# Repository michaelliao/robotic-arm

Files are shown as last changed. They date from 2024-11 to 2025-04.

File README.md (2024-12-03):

# Robotic Arm

Robotic Arm是一个开源机械臂，采用ESP32-C3芯片通过PCA9685芯片控制4路舵机，使用Xbox兼容手柄遥控。

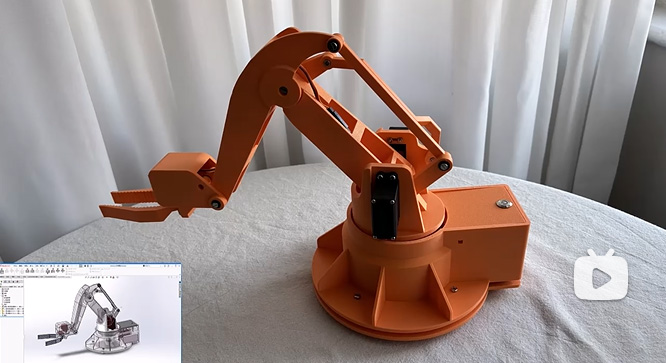
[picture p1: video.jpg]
video (https://www.bilibili.com/video/BV1EWz1YaE7P/)


## 目录结构说明

- solidworks-model：SolidWorks 2023模型源文件。
- 3d-printable：可用于3D打印的模型文件，由SolidWorks导出：
  - step：Step格式（推荐使用，如果打印机支持Step格式）。
  - stl：STL格式（通用可打印格式）。
  - 3mf：可直接打印的3D打印格式。
- esp32-controller：ESP-IDF工程源码。
- docs：相关资料。

## 设计

使用SolidWorks 2023设计建模。

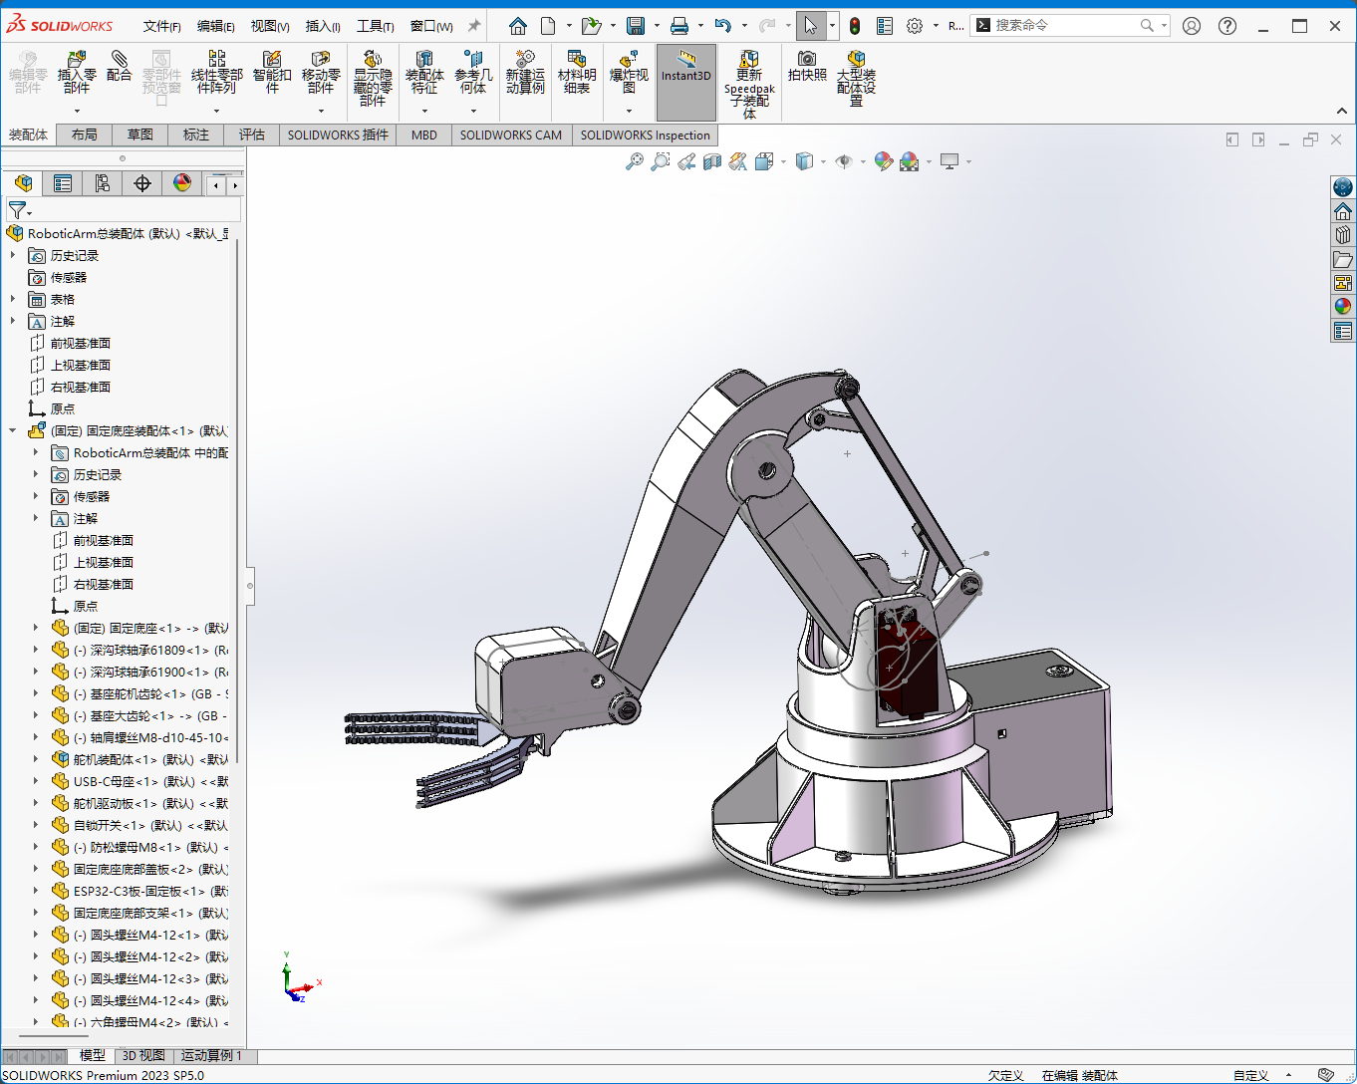
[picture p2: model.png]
solidworks-model


## 控制

使用MG996Rx3、MG90S舵机，ESP32-C3主控，PCA9685舵机驱动板，Xbox兼容手柄。

## 文档

[软件设计文档](https://liaoxuefeng.com/blogs/all/2024-12-03-robotic-arm/index.html)

## 物料清单

| 名称 | 数量 | 参考单价 (CNY) | 参考购买链接 | 说明 |
|---|---|----|---|---|
| 3D打印零件 | 1 | 70 | 使用FDM 3D打印 | 约700g PLA材料 |
| 深沟球轴承61809 | 1 | 4 | https://detail.tmall.com/item.htm?id=558165998149&skuId=3632300271694 | 固定底座旋转轴(上) |
| 深沟球轴承61900 | 1 | 1 | https://detail.tmall.com/item.htm?id=558028332089&skuId=3466348596124 | 固定底座旋转轴(下) |
| 深沟球轴承619-5 | 2 | 1 | https://detail.tmall.com/item.htm?id=665677732947&skuId=4803499105837 | 旋转底座主摇杆 |
| igus法兰轴承GFM-04050-04 | 20 | 4 | https://item.taobao.com/item.htm?id=577055358668&skuId=3973097699261 | 连接杆 |
| igus法兰轴承GFM-0506-05  | 4  | 3 | https://item.taobao.com/item.htm?id=577055358668&skuId=3917924689834 | 连接杆 |
| 轴肩螺丝M8-d10-45-10 | 1 | 3 | https://item.taobao.com/item.htm?id=727328728239&skuId=5220634259143 | 固定底座主杆 |
| 轴肩螺丝M4-d5-30-5 | 1 | 2 | https://item.taobao.com/item.htm?id=727328728239&skuId=5220634259095 | |
| 轴肩螺丝M4-d5-20-5 | 1 | 1 | https://item.taobao.com/item.htm?id=727328728239&skuId=5220634259093 | |
| 轴肩螺丝M3-d4-20-4 | 3 | 2 | https://item.taobao.com/item.htm?id=727328728239&skuId=5220634259082 | |
| 轴肩螺丝M3-d4-12-4 | 7 | 2 | https://item.taobao.com/item.htm?id=727328728239&skuId=5220634259079 | |
| 防松螺母M8 | 1 | 1 | https://item.taobao.com/item.htm?id=39801137771&skuId=3179651418712 | |
| 防松螺母M4 | 2 | 1 | https://item.taobao.com/item.htm?id=39801137771&skuId=3179651418702 | |
| 防松螺母M3 | 10 | 1 | https://item.taobao.com/item.htm?id=39801137771&skuId=3179651418705 | |
| 圆头螺丝M4-12 | 4 | 1 | https://item.taobao.com/item.html?id=559706384805&skuId=4924704353913 | |
| 圆头螺丝M2.5-12 | 12 | 1 | https://item.taobao.com/item.html?id=559706384805&skuId=4924704353893 | 用于安装MG996R舵机 |
| 圆头螺丝M2-20 | 2 | 1 | https://item.taobao.com/item.html?id=559706384805&skuId=4924704353971 | 用于安装MG90S舵机 |
| 圆头螺丝M2-8 | 2 | 1 | https://item.taobao.com/item.html?id=559706384805&skuId=4924704353888 | |
| 六角螺母M4 | 4 | 1 | https://item.taobao.com/item.htm?id=39801137771&skuId=3179651418702 | |
| 六角螺母M2.5 | 12 | 1 | https://item.taobao.com/item.htm?id=39801137771&skuId=3179950216671 | |
| 六角螺母M2 | 2 | 1 | https://item.taobao.com/item.htm?id=39801137771&skuId=3179950216672 | |
| MG90S/180度 | 1 | 17  | https://detail.tmall.com/item.htm?id=530629424244&skuId=4179287423050 | 用于前爪的微型舵机 |
| MG996R/180度 | 3 | 23  | https://detail.tmall.com/item.htm?id=530629424244&skuId=4179287423040 | 用于固定底座和移动底座的小型舵机 |
| ESP32-C3开发板 | 1 | 20 | https://detail.tmall.com/item.htm?id=802840084513&skuId=5465032488648 | 机械臂控制MCU，内置WiFi/2.4G和蓝牙BLE 5 |
| 16路PWM舵机驱动板 | 1 | 27 | https://detail.tmall.com/item.htm?id=624505789589&skuId=5054325653554 | 使用I2C接口的舵机驱动板，最多能同时驱动16路舵机 |
| 固定卡扣 | 1 | 6 | https://item.taobao.com/item.htm?id=812206553246&skuId=5676343543601 | 将机械臂固定在桌面 |
| 12mm自锁开关 | 1 | 5 | https://detail.tmall.com/item.htm?id=607769066907&skuId=5258355114246 | 机械臂电源开关 |
| 12mm自锁开关连接器 | 1 | 2 | https://detail.tmall.com/item.htm?id=607769066907&skuId=4419711093384 | 建议购买，免去焊接 |
| 盖世小鸡启明星游戏手柄 | 1 | 80 | https://detail.tmall.com/item.htm?id=749611763829&skuId=5169816701870 | Xbox兼容手柄，支持蓝牙BLE 5 |
| 10cm杜邦线 | 3 | 3 | https://detail.tmall.com/item.htm?id=14466195609 | 建议购买公对公、公对母、母对母排线，免去焊接 |

## 参考资料

- [阿奇SolidWorks教程](https://www.bilibili.com/video/BV1iw411Z7HZ/)
- [阿奇讲SolidWorks机械臂](https://www.bilibili.com/cheese/play/ss865)
- [ESP32教程（基于ESP-IDF）](https://www.bilibili.com/video/BV1eRg7exEcT/)
- [乐鑫全球开发者大会｜嵌入式系统中的低功耗蓝牙开发](https://www.bilibili.com/video/BV1kh4y1Y7GU/)
- [ESP32 PWM Driver](https://github.com/brainelectronics/esp32-pca9685)

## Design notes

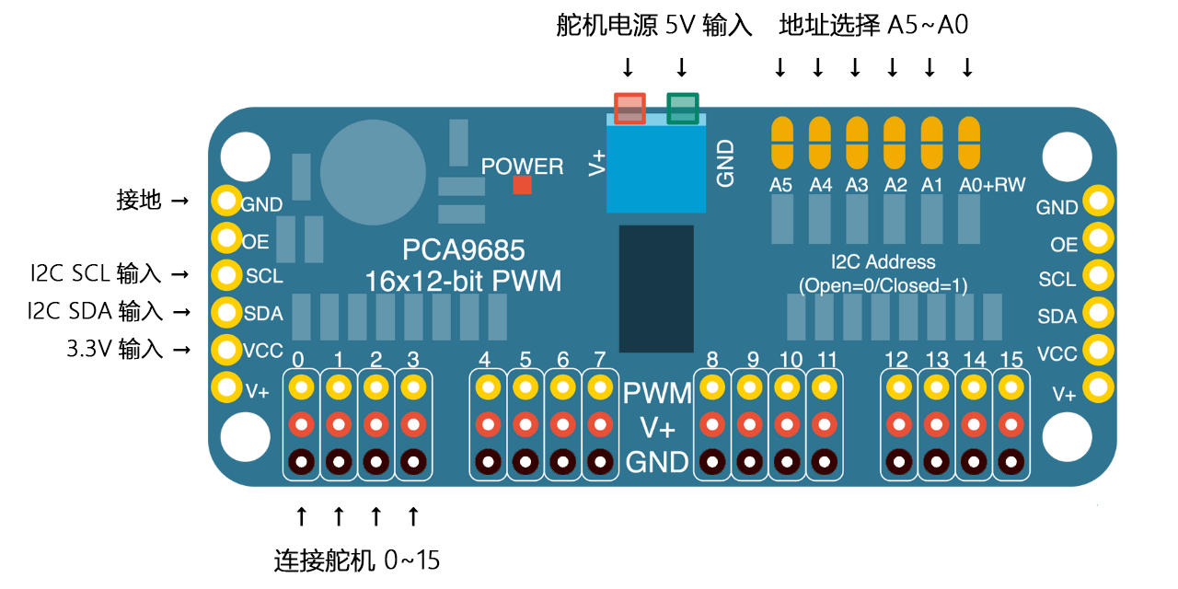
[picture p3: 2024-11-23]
docs/pca9685.png

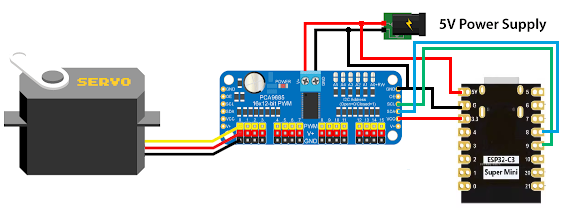
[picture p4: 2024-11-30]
docs/esp32c3-pca9685-servo.png

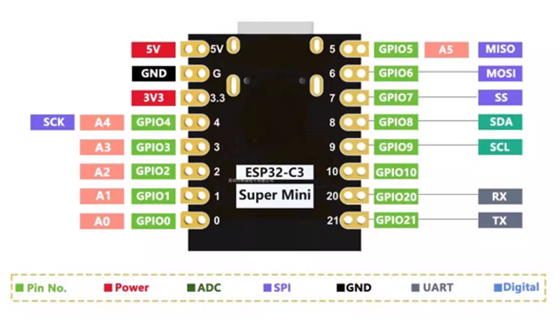
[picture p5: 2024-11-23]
docs/esp32c3.png

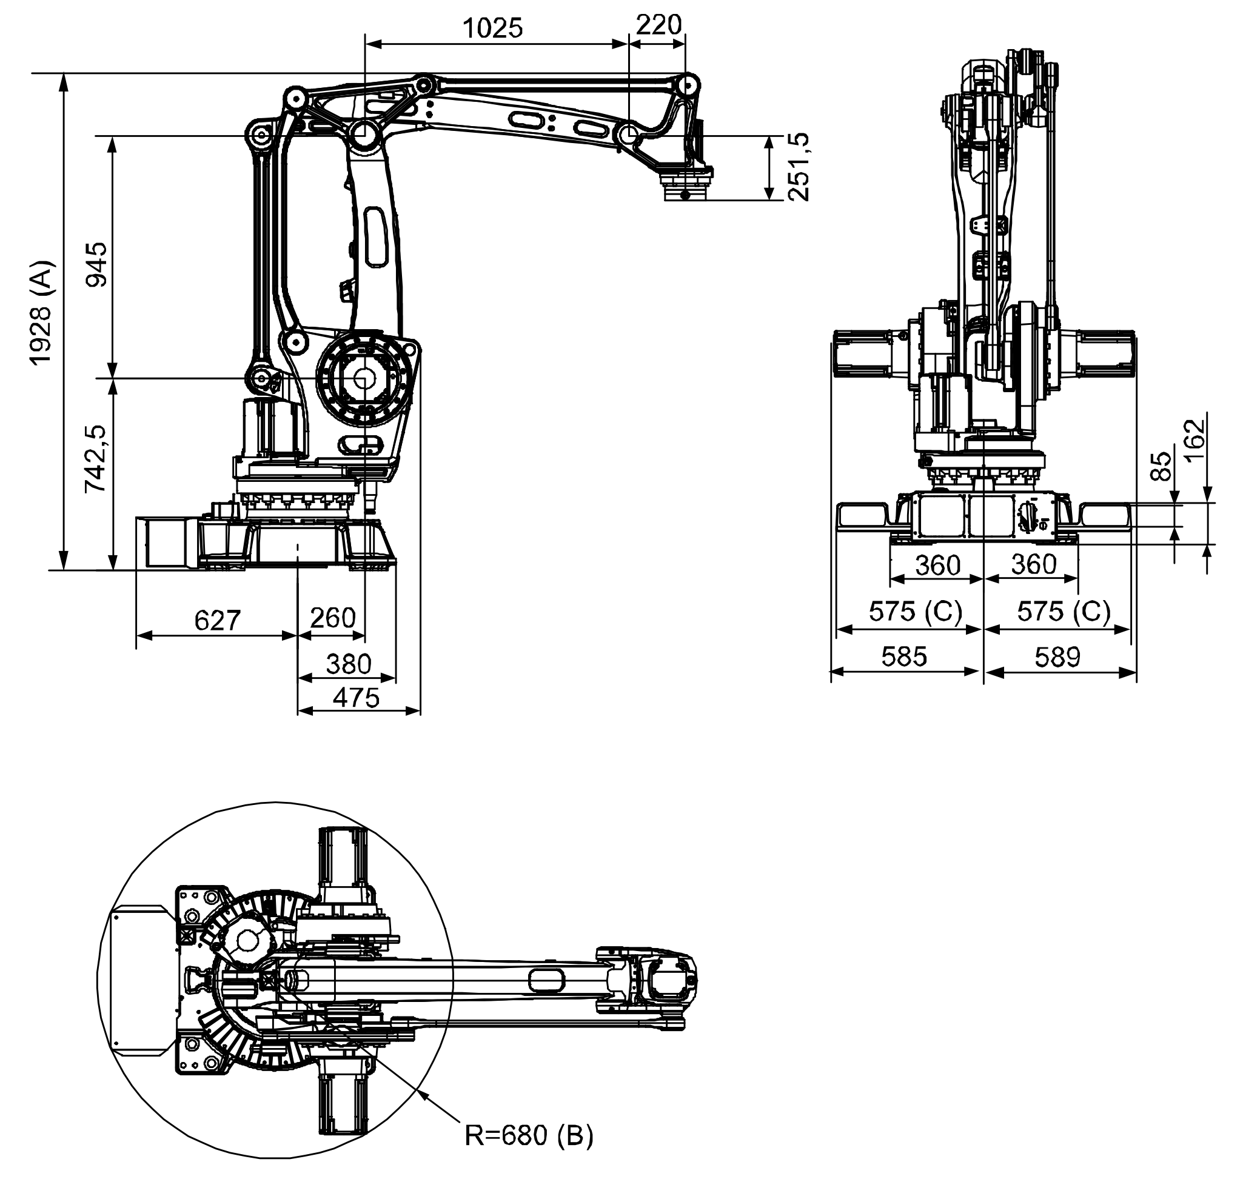
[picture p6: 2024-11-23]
docs/irb-460.png

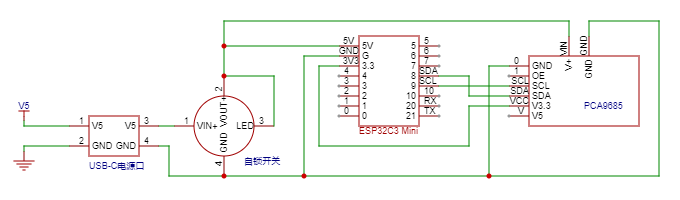
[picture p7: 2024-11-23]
docs/电路图.png

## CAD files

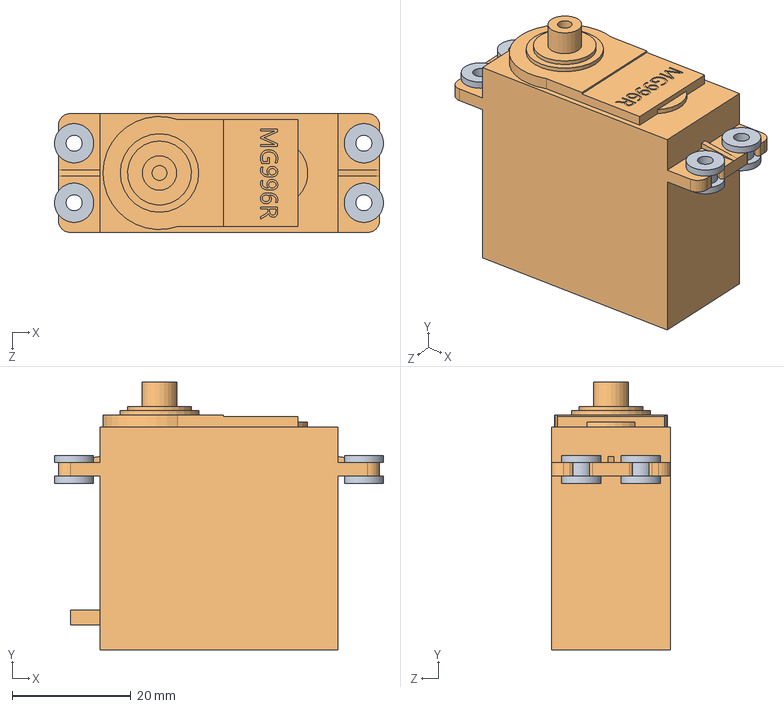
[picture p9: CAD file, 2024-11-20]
solidworks-model/舵机/舵机装配体.SLDASM
55.3 x 45.0 x 20.0 mm
MG996R
舵机橡胶圈 x 4

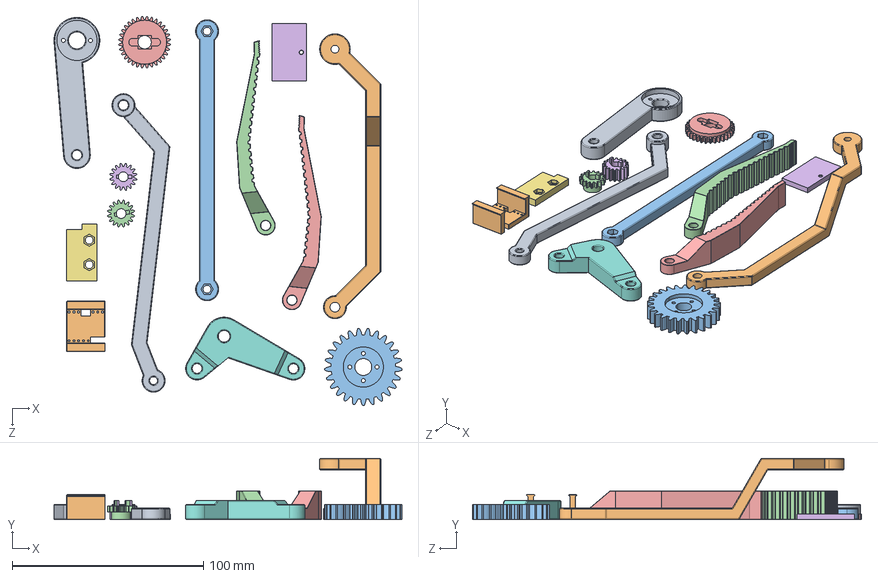
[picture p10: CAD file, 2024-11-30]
3d-printable/step/打印件2.STEP
182.1 x 32.0 x 203.8 mm
C轴摇杆
ESP32-C3板-固定板
基座舵机齿轮_GB - Spur gear 1.5M 25T 20PA 8FW ---S25A75H50L1.0N
夹爪齿轮-薄_GB - Spur gear 0.8M 16T 20PA 3FW ---S16A75H50L1.0N
夹爪齿轮-舵机_GB - Spur gear 0.8M 32T 20PA 3FW ---S32A75H50L1.0N
夹爪齿轮-厚_GB - Spur gear 0.8M 16T 20PA 7FW ---S16A75H50L1.0N
夹爪支架内部齿轮固定板
三角连杆
上水平连杆
下水平连杆
C轴连杆
夹爪C-右
夹爪C-左
夹爪支架内部舵机固定板

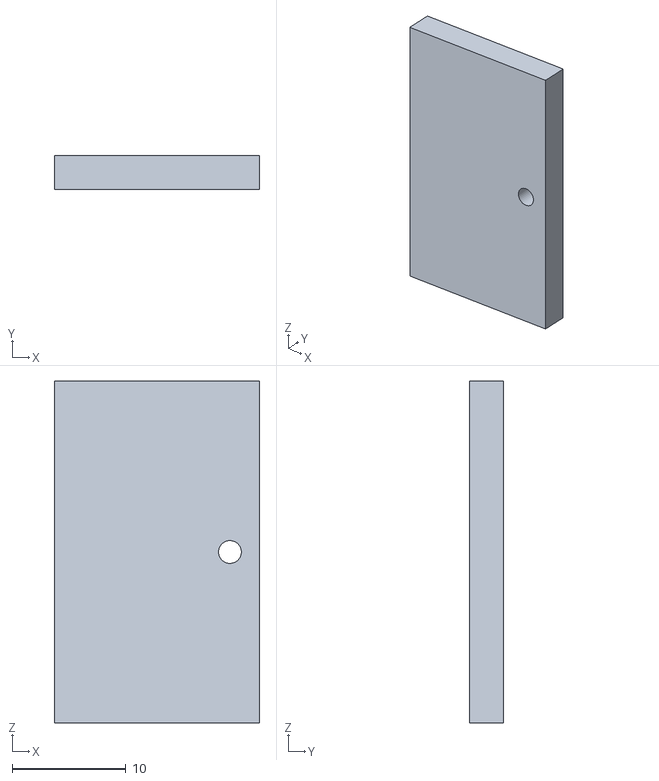
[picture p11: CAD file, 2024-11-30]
3d-printable/stl/打印装配体 - 夹爪支架内部舵机固定板-1.STL
18.0 x 3.00 x 30.0

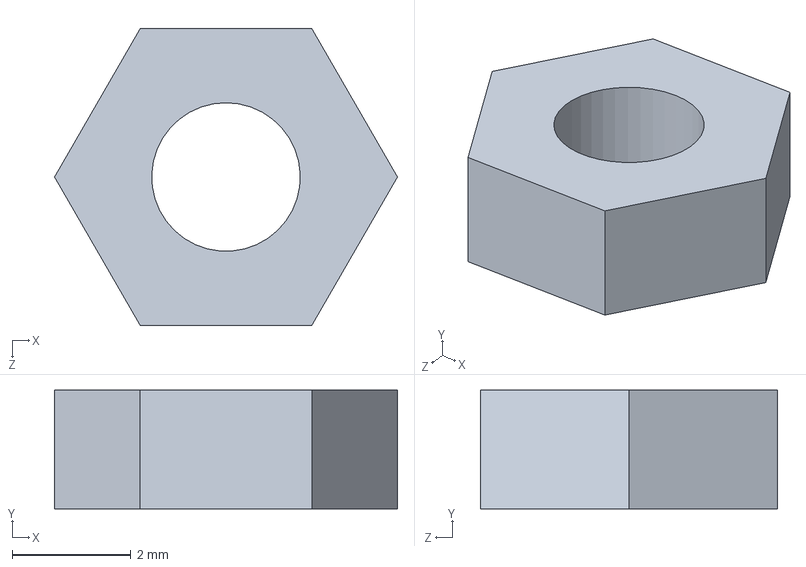
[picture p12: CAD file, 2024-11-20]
solidworks-model/五金件/六角螺母M2.5.SLDPRT
5.77 x 2.00 x 5.00 mm

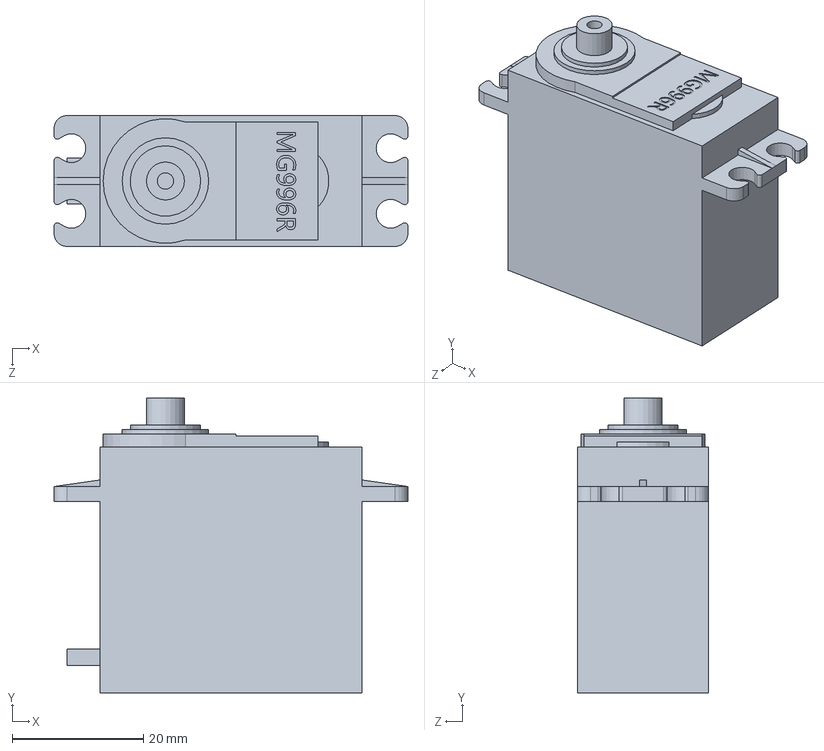
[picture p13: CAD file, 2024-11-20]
solidworks-model/舵机/MG996R.SLDPRT
54.0 x 45.0 x 20.0 mm

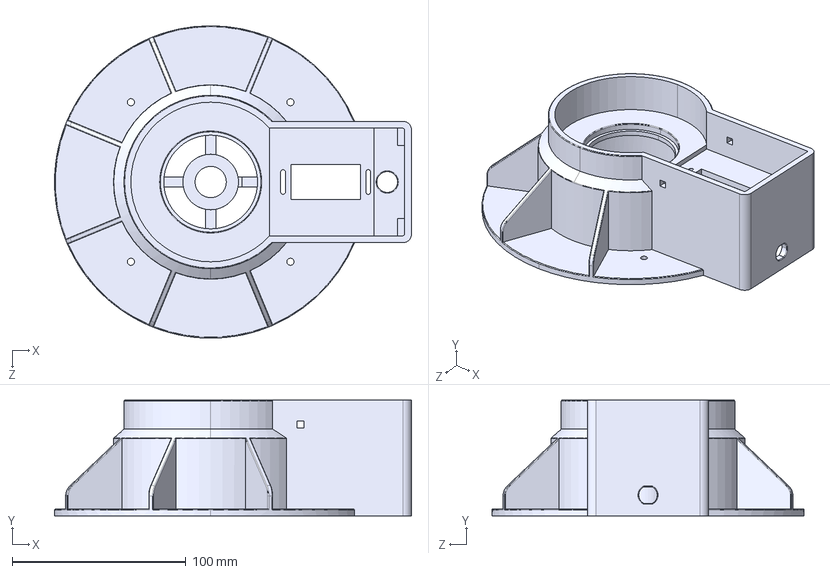
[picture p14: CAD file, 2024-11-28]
3d-printable/step/打印件1.STEP
205.7 x 66.7 x 180.0 mm

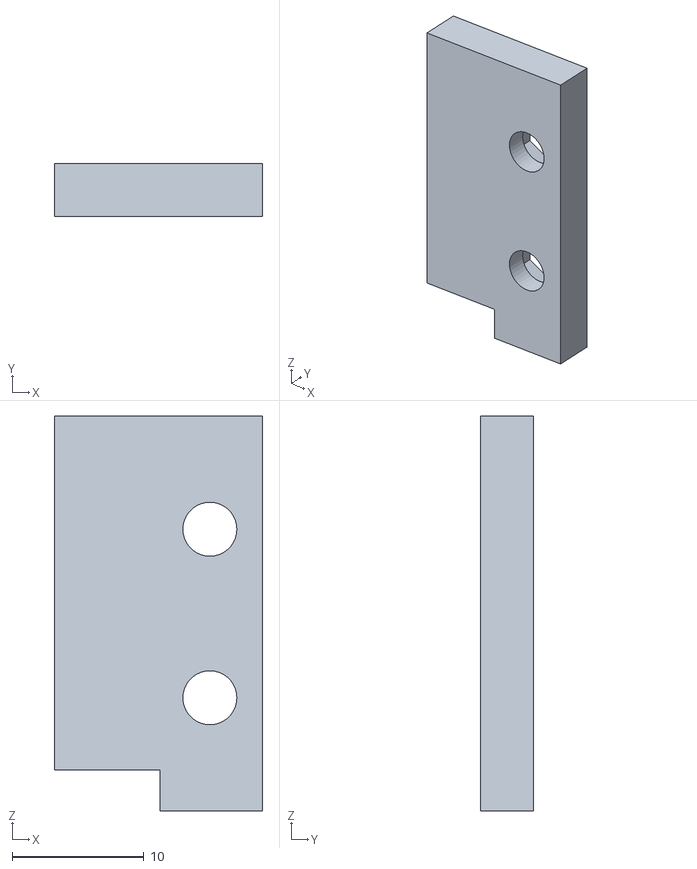
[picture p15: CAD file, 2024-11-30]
3d-printable/stl/打印装配体 - 夹爪支架内部齿轮固定板-1.STL
15.8 x 4.00 x 30.0

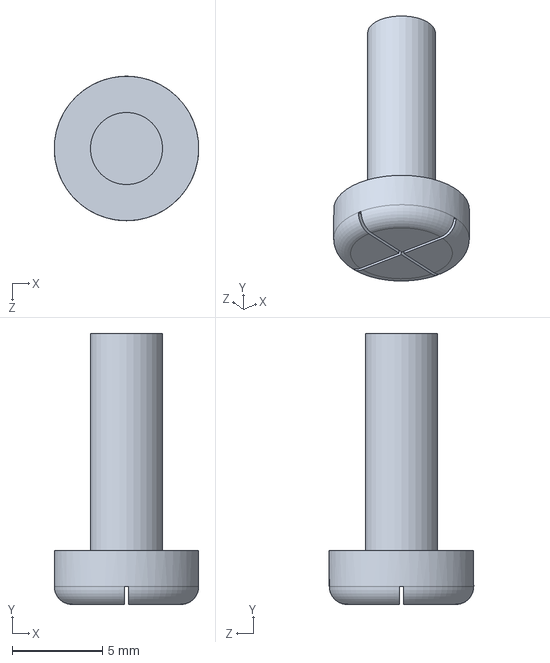
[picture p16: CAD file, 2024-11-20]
solidworks-model/五金件/圆头螺丝M4-12.SLDPRT
8.00 x 15.0 x 8.00 mm

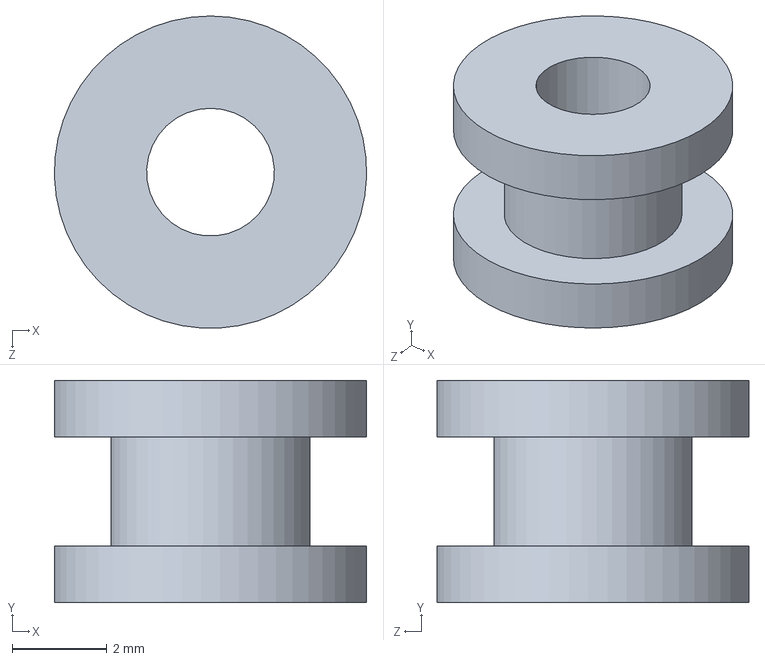
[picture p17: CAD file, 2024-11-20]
solidworks-model/舵机/舵机橡胶圈.SLDPRT
6.60 x 4.70 x 6.59 mm

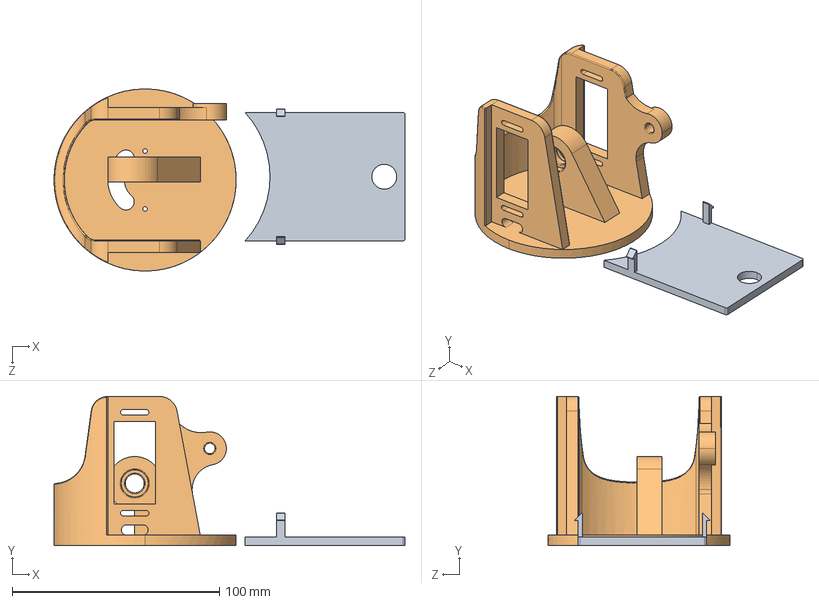
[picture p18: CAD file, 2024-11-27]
3d-printable/step/打印件6.STEP
169.5 x 72.0 x 88.0 mm
固定底座底部盖板
旋转底座

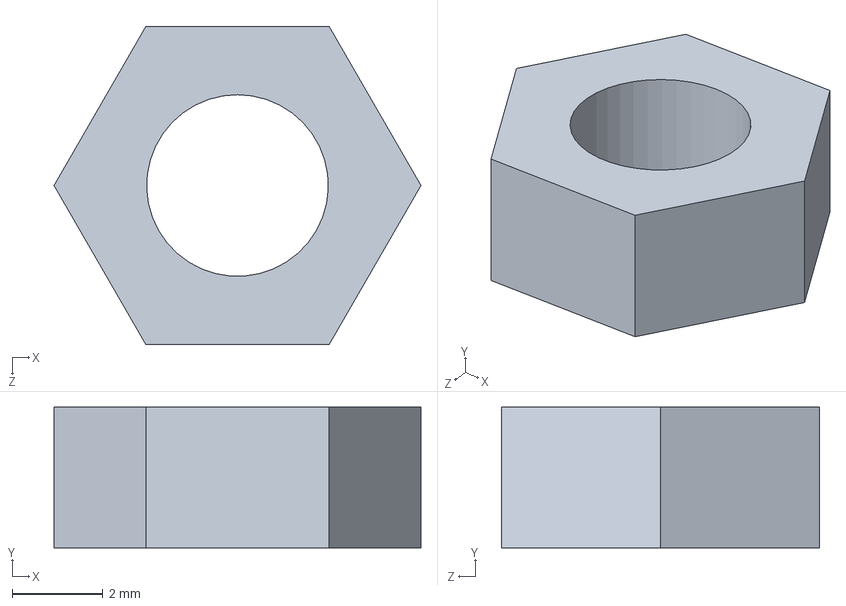
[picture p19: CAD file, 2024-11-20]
solidworks-model/五金件/六角螺母M4.SLDPRT
8.08 x 3.10 x 7.00 mm

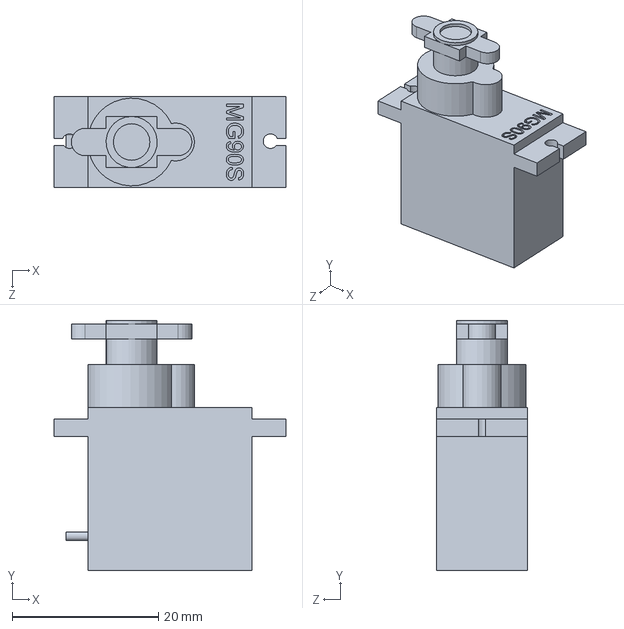
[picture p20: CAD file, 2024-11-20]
solidworks-model/舵机/MG90S.SLDPRT
31.7 x 34.2 x 12.5 mm

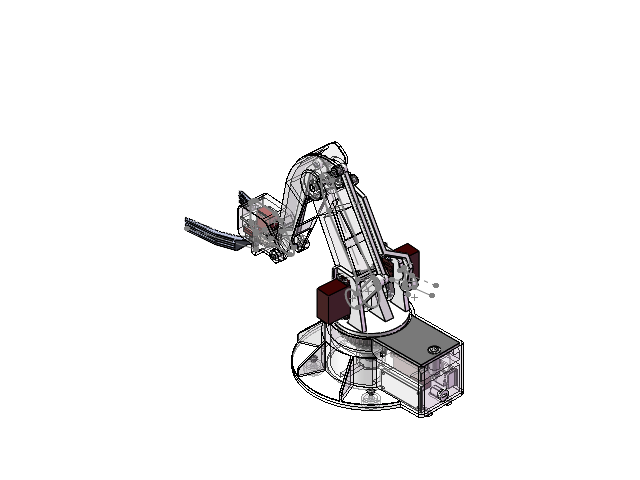
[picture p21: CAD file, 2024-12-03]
solidworks-model/RoboticArm总装配体.SLDASM
固定底座
深沟球轴承61809
深沟球轴承61900
基座舵机齿轮
基座大齿轮
轴肩螺丝M8-d10-45-10
MG996R x 3
舵机橡胶圈 x 12
舵机圆盘 x 3
USB-C母座
舵机驱动板
自锁开关
防松螺母M8
固定底座底部盖板
ESP32-C3板-固定板
固定底座底部支架
圆头螺丝M4-12 x 4
六角螺母M4 x 4
圆头螺丝M2.5-12 x 12
六角螺母M2.5 x 12
旋转底座
C轴摇杆
轴肩螺丝M4-d5-20-5
防松螺母M4 x 2
深沟球轴承619-5 x 2
BC连杆
CD连杆
C轴连杆
上水平连杆
下水平连杆
夹爪支架
MG90S
夹爪齿轮-薄
夹爪齿轮-厚
夹爪齿轮-舵机
轴肩螺丝M3-d4-20-4 x 3
防松螺母M3 x 10
轴肩螺丝M3-d4-12-4 x 7
夹爪-右
夹爪-左
夹爪支架内部齿轮固定板
圆头螺丝M2-8 x 2
夹爪支架内部舵机固定板
法兰轴承d4-GFM-04050-04 x 12
法兰轴承d5-GFM-0506-05 x 4
三角连杆
轴肩螺丝M4-d5-30-5
圆头螺丝M2-20 x 2

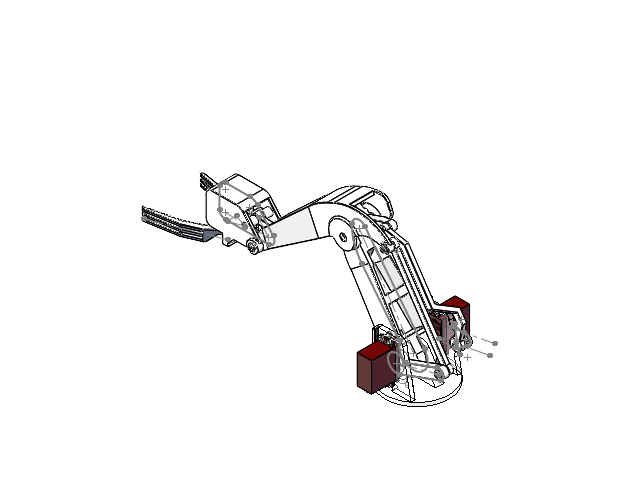
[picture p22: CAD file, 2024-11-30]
solidworks-model/旋转底座装配体.SLDASM
旋转底座
MG996R x 2
舵机橡胶圈 x 8
舵机圆盘 x 2
C轴摇杆
轴肩螺丝M4-d5-20-5
防松螺母M4 x 2
深沟球轴承619-5 x 2
BC连杆
CD连杆
C轴连杆
上水平连杆
下水平连杆
夹爪支架
MG90S
夹爪齿轮-薄
夹爪齿轮-厚
夹爪齿轮-舵机
法兰轴承d4-GFM-04050-04 x 20
轴肩螺丝M3-d4-20-4 x 3
防松螺母M3 x 10
轴肩螺丝M3-d4-12-4 x 7
夹爪-右
夹爪-左
夹爪支架内部齿轮固定板
圆头螺丝M2-8 x 2
夹爪支架内部舵机固定板
法兰轴承d5-GFM-0506-05 x 4
三角连杆
轴肩螺丝M4-d5-30-5
圆头螺丝M2.5-12 x 8
六角螺母M2.5 x 8

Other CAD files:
solidworks-model/夹爪装配体.SLDASM
solidworks-model/固定底座装配体.SLDASM
solidworks-model/打印装配体.SLDASM
3d-printable/stl/打印装配体 - 固定底座-1.STL
3d-printable/step/打印件3.STEP
3d-printable/step/打印件4.STEP
3d-printable/step/打印件5.STEP
3d-printable/step/打印测试.STEP
3d-printable/stl/打印装配体 - BC连杆-1.STL
3d-printable/stl/打印装配体 - CD连杆-1.STL
3d-printable/stl/打印装配体 - C轴摇杆-1.STL
3d-printable/stl/打印装配体 - C轴连杆-2.STL
3d-printable/stl/打印装配体 - ESP32-C3板-固定板-1.STL
3d-printable/stl/打印装配体 - 三角连杆-1.STL
3d-printable/stl/打印装配体 - 上水平连杆-1.STL
3d-printable/stl/打印装配体 - 下水平连杆-1.STL
3d-printable/stl/打印装配体 - 固定底座底部支架-1.STL
3d-printable/stl/打印装配体 - 固定底座底部盖板-1.STL
3d-printable/stl/打印装配体 - 基座大齿轮-1.STL
3d-printable/stl/打印装配体 - 基座舵机齿轮-1.STL
3d-printable/stl/打印装配体 - 夹爪C-右-1.STL
3d-printable/stl/打印装配体 - 夹爪C-左-1.STL
3d-printable/stl/打印装配体 - 夹爪支架-1.STL
3d-printable/stl/打印装配体 - 夹爪齿轮-厚-1.STL
3d-printable/stl/打印装配体 - 夹爪齿轮-舵机-1.STL
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

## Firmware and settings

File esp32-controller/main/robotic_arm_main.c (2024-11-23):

/*
 * SPDX-FileCopyrightText: 2021-2024 Espressif Systems (Shanghai) CO LTD
 *
 * SPDX-License-Identifier: Unlicense OR CC0-1.0
 */

#include <stdio.h>
#include <stdlib.h>
#include <string.h>

#include <driver/i2c.h>
#include "freertos/FreeRTOS.h"
#include "freertos/task.h"
#include "freertos/queue.h"
#include "freertos/event_groups.h"
#include "esp_chip_info.h"
#include "esp_flash.h"
#include "esp_system.h"
#include "esp_timer.h"
#include "esp_wifi.h"
#include "esp_event.h"
#include "esp_log.h"
#include "nvs_flash.h"
#include "esp_bt.h"

#if CONFIG_BT_NIMBLE_ENABLED
#include "host/ble_hs.h"
#include "nimble/nimble_port.h"
#include "nimble/nimble_port_freertos.h"
#else
#include "esp_bt_defs.h"
#include "esp_gap_ble_api.h"
#include "esp_gatts_api.h"
#include "esp_gatt_defs.h"
#include "esp_bt_main.h"
#include "esp_bt_device.h"
#endif

#if CONFIG_BT_NIMBLE_ENABLED
#include "host/ble_hs.h"
#include "nimble/nimble_port.h"
#include "nimble/nimble_port_freertos.h"
#define ESP_BD_ADDR_STR         "%02x:%02x:%02x:%02x:%02x:%02x"
#define ESP_BD_ADDR_HEX(addr)   addr[0], addr[1], addr[2], addr[3], addr[4], addr[5]
#else
#include "esp_bt_defs.h"
#include "esp_gap_ble_api.h"
#include "esp_gatts_api.h"
#include "esp_gatt_defs.h"
#include "esp_bt_main.h"
#include "esp_bt_device.h"
#endif

#include "esp_hidh.h"
#include "esp_hid_gap.h"

#include "pca9685.h"

// 注意: 将IO管脚修改为实际连接的PIN:
#define RA_I2C_MASTER_SDA_IO 8
#define RA_I2C_MASTER_SCL_IO 9

// 注意: I2C设备地址默认为0x40, 如有修改, 需改为实际地址:
#define RA_I2C_ADDRESS 0x40

// PWM频率为50Hz:
#define RA_PWM_FREQ 50

// PWM周期为20ms=20000us:
#define RA_SERVO_PWM_TIME (uint32_t)20000
// PWM脉冲时间为0.5~2.5ms=500~2500us:
#define RA_SERVO_PULSE_MIN (uint32_t)500
#define RA_SERVO_PULSE_MAX (uint32_t)2500
// 计算PWM对应的范围:
#define RA_SERVO_PWM_MIN (uint32_t)(4096 * RA_SERVO_PULSE_MIN / RA_SERVO_PWM_TIME - 1)
#define RA_SERVO_PWM_MAX (uint32_t)(4096 * RA_SERVO_PULSE_MAX / RA_SERVO_PWM_TIME - 1)
#define RA_SERVO_PWM_MID (uint32_t)((RA_SERVO_PWM_MIN + RA_SERVO_PWM_MAX) / 2)
#define RA_SERVO_PWM_RANGE (uint32_t)(RA_SERVO_PWM_MAX - RA_SERVO_PWM_MIN + 1)

// 角度范围:
#define RA_SERVO_ANGLE_RANGE (uint32_t)180

// I2C频率=100KHz:
#define RA_I2C_MASTER_FREQ 100000

// 舵机索引号:
#define RA_SERVO_A 0
#define RA_SERVO_B 1
#define RA_SERVO_C 2
#define RA_SERVO_D 3

#ifndef APP_CPU_NUM
#define APP_CPU_NUM PRO_CPU_NUM
#endif

// XBox手柄按钮:
#define XBOX_BUTTON_A 0x01
#define XBOX_BUTTON_B 0x02
#define XBOX_BUTTON_X 0x08
#define XBOX_BUTTON_Y 0x10
#define XBOX_BUTTON_L1 0x40
#define XBOX_BUTTON_R1 0x80
#define XBOX_EX_BUTTON_VIEW 0x04
#define XBOX_EX_BUTTON_MENU 0x08

#define CTRL_INPUT_DATA_LENGTH 16

#define SCAN_DURATION_SECONDS 5

static const char *TAG_HID = "HID";
static const char *TAG_PWM = "PWM";

// 根据手柄名称进行过滤,注意大小写:
static const char *CTRL_NAME = "Xbox Wireless Controller";

// 手柄输入队列:
QueueHandle_t ctrl_input_queue = NULL;

// 手柄输入数据:
// https://support.xbox.com/en-US/help/hardware-network/controller/xbox-one-wireless-controller
typedef struct __attribute__((packed)) {
    uint16_t left_stick_x; // 左摇杆
    uint16_t left_stick_y;
    uint16_t right_stick_x; // 右摇杆
    uint16_t right_stick_y;
    uint8_t left_trigger; // 左上L2按钮
    uint8_t left_trigger_level;
    uint8_t right_trigger; // 右上R2按钮
    uint8_t right_trigger_level;
    uint8_t any_1;
    uint8_t buttons; // A,B,X,Y,L1,R1按钮
    uint8_t ex_buttons; // VIEW, MENU按钮
    uint8_t any_2;
} ctrl_input_data_t;

typedef struct {
    // 允许的角度范围,例如60~120:
    int16_t min_angle;
    int16_t max_angle;
    // 初始角度,理想状态是90,但允许误差,如实际为95:
    int16_t initial_angle;
    // 目标角度:
    int16_t target_angle;
} servo_t;

static servo_t servos[4];

// 连接状态:
enum CTRL_STATE
{
    SCANNING, // 正在扫描
    OPENING, // 正在打开
    INPUT // 正常输入
};

static enum CTRL_STATE ctrl_state = SCANNING;

// 记录上一次的手柄输入数据:
static ctrl_input_data_t ctrl_input_data;
// 记录上一次的手柄输入时间:
static int64_t ctrl_input_time = 0;

static char *bda2str(esp_bd_addr_t bda, char *str, size_t size)
{
    if (bda == NULL || str == NULL || size < 18) {
        return NULL;
    }

    uint8_t *p = bda;
    sprintf(str, "%02x:%02x:%02x:%02x:%02x:%02x",
            p[0], p[1], p[2], p[3], p[4], p[5]);
    return str;
}

// 处理蓝牙手柄输入:
void hidh_callback(void *handler_args, esp_event_base_t base, int32_t id, void *event_data)
{
    esp_hidh_event_t event = (esp_hidh_event_t)id;
    esp_hidh_event_data_t *param = (esp_hidh_event_data_t *)event_data;

    switch (event) {
    case ESP_HIDH_OPEN_EVENT: {
        if (param->open.status == ESP_OK) {
            const uint8_t *bda = esp_hidh_dev_bda_get(param->open.dev);
            ESP_LOGI(TAG_HID, ESP_BD_ADDR_STR " OPEN: %s", ESP_BD_ADDR_HEX(bda), esp_hidh_dev_name_get(param->open.dev));
            esp_hidh_dev_dump(param->open.dev, stdout);
            ctrl_state = INPUT;
        } else {
            ESP_LOGE(TAG_HID, " OPEN failed!");
            ctrl_state = SCANNING;
        }
        break;
    }
    case ESP_HIDH_BATTERY_EVENT: {
        const uint8_t *bda = esp_hidh_dev_bda_get(param->battery.dev);
        ESP_LOGI(TAG_HID, ESP_BD_ADDR_STR " BATTERY: %d%%", ESP_BD_ADDR_HEX(bda), param->battery.level);
        break;
    }
    case ESP_HIDH_INPUT_EVENT: {
        // 处理手柄输入:
        const uint8_t *bda = esp_hidh_dev_bda_get(param->input.dev);
        if (param->input.length == CTRL_INPUT_DATA_LENGTH) {
            // 每200ms采样输入:
            int64_t now = esp_timer_get_time();
            if (now - ctrl_input_time > 200000) {
                // 复制输入数据并发送消息到队列:
                memcpy(&ctrl_input_data, (char *) param->input.data, CTRL_INPUT_DATA_LENGTH);
                xQueueSend(ctrl_input_queue, &ctrl_input_data, 0); // 如果上一次的输入数据还未处理，则不等待直接丢弃
                ESP_LOGI(TAG_HID, ESP_BD_ADDR_STR " INPUT: %8s, MAP: %2u, ID: %3u, Len: %d, Data:", ESP_BD_ADDR_HEX(bda), esp_hid_usage_str(param->input.usage), param->input.map_index, param->input.report_id, param->input.length);
                ESP_LOG_BUFFER_HEX(TAG_HID, param->input.data, param->input.length);
                ctrl_input_time = now;
            }
        } else {
            ESP_LOGW(TAG_HID, "invalid input length: %d", param->input.length);
        }
        break;
    }
    case ESP_HIDH_FEATURE_EVENT: {
        const uint8_t *bda = esp_hidh_dev_bda_get(param->feature.dev);
        ESP_LOGI(TAG_HID, ESP_BD_ADDR_STR " FEATURE: %8s, MAP: %2u, ID: %3u, Len: %d", ESP_BD_ADDR_HEX(bda),
                 esp_hid_usage_str(param->feature.usage), param->feature.map_index, param->feature.report_id,
                 param->feature.length);
        ESP_LOG_BUFFER_HEX(TAG_HID, param->feature.data, param->feature.length);
        break;
    }
    case ESP_HIDH_CLOSE_EVENT: {
        const uint8_t *bda = esp_hidh_dev_bda_get(param->close.dev);
        ESP_LOGI(TAG_HID, ESP_BD_ADDR_STR " CLOSE: %s", ESP_BD_ADDR_HEX(bda), esp_hidh_dev_name_get(param->close.dev));
        ctrl_state = SCANNING;
        break;
    }
    default:
        ESP_LOGI(TAG_HID, "default EVENT: %d", event);
        break;
    }
}

void hid_scan()
{
    size_t results_len = 0;
    esp_hid_scan_result_t *results = NULL;
    ESP_LOGI(TAG_HID, "SCAN...");
    //start scan for HID devices
    esp_hid_scan(SCAN_DURATION_SECONDS, &results_len, &results);
    ESP_LOGI(TAG_HID, "SCAN: %u results", results_len);
    if (results_len) {
        esp_hid_scan_result_t *r = results;
        esp_hid_scan_result_t *cr = NULL;
        while (r) {
            printf("  %s: " ESP_BD_ADDR_STR ", ", (r->transport == ESP_HID_TRANSPORT_BLE) ? "BLE" : "BT ", ESP_BD_ADDR_HEX(r->bda));
            printf("RSSI: %d, ", r->rssi);
            printf("USAGE: %s, ", esp_hid_usage_str(r->usage));
#if CONFIG_BT_BLE_ENABLED
            if (r->transport == ESP_HID_TRANSPORT_BLE) {
                if (r->name && strcmp(r->name, CTRL_NAME) == 0) {
                    cr = r;
                }
                printf("APPEARANCE: 0x%04x, ", r->ble.appearance);
                printf("ADDR_TYPE: '%s', ", ble_addr_type_str(r->ble.addr_type));
            }
#endif /* CONFIG_BT_BLE_ENABLED */
#if CONFIG_BT_NIMBLE_ENABLED
            if (r->transport == ESP_HID_TRANSPORT_BLE) {
                if (r->name && strcmp(r->name, CTRL_NAME) == 0) {
                    cr = r;
                }
                printf("APPEARANCE: 0x%04x, ", r->ble.appearance);
                printf("ADDR_TYPE: '%d', ", r->ble.addr_type);
            }
#endif /* CONFIG_BT_BLE_ENABLED */
#if CONFIG_BT_HID_HOST_ENABLED
            if (r->transport == ESP_HID_TRANSPORT_BT) {
                if (r->name && strcmp(r->name, CTRL_NAME) == 0) {
                    cr = r;
                }
                printf("COD: %s[", esp_hid_cod_major_str(r->bt.cod.major));
                esp_hid_cod_minor_print(r->bt.cod.minor, stdout);
                printf("] srv 0x%03x, ", r->bt.cod.service);
                print_uuid(&r->bt.uuid);
                printf(", ");
            }
#endif /* CONFIG_BT_HID_HOST_ENABLED */
            printf("NAME: %s ", r->name ? r->name : "");
            printf("\n");
            r = r->next;
        }
        if (cr) {
            //open the last result
            ctrl_state = OPENING;
            esp_hidh_dev_open(cr->bda, cr->transport, cr->ble.addr_type);
        }
        //free the results
        esp_hid_scan_results_free(results);
    }
}

void hid_scan_task(void *pvParameters)
{
    for (;;) {
        vTaskDelay(5000 / portTICK_PERIOD_MS);
        if (ctrl_state == SCANNING) {
            hid_scan();
        }
    }
}

#if CONFIG_BT_NIMBLE_ENABLED
void ble_hid_host_task(void *param)
{
    ESP_LOGI(TAG_HID, "BLE Host Task Started");
    /* This function will return only when nimble_port_stop() is executed */
    nimble_port_run();

    nimble_port_freertos_deinit();
}
void ble_store_config_init(void);
#endif

static void init_i2c_master()
{
    ESP_LOGI(TAG_HID, "init i2c master: SDA = %d, SCL = %d.", RA_I2C_MASTER_SDA_IO, RA_I2C_MASTER_SCL_IO);
    i2c_config_t conf;
    conf.mode = I2C_MODE_MASTER;
    conf.sda_io_num = RA_I2C_MASTER_SDA_IO;
    conf.scl_io_num = RA_I2C_MASTER_SCL_IO;
    conf.sda_pullup_en = GPIO_PULLUP_ENABLE;
    conf.scl_pullup_en = GPIO_PULLUP_ENABLE;
    conf.master.clk_speed = RA_I2C_MASTER_FREQ;

    ESP_ERROR_CHECK(i2c_param_config(I2C_NUM_0, &conf));
    ESP_ERROR_CHECK(i2c_driver_install(I2C_NUM_0, conf.mode, 0, 0, 0));
}

static void init_chip()
{
    /* Print chip information */
    esp_chip_info_t chip_info;
    uint32_t flash_size;
    esp_chip_info(&chip_info);
    printf("This is %s chip with %d CPU core(s), %s%s%s%s, ",
           CONFIG_IDF_TARGET,
           chip_info.cores,
           (chip_info.features & CHIP_FEATURE_WIFI_BGN) ? "WiFi/" : "",
           (chip_info.features & CHIP_FEATURE_BT) ? "BT" : "",
           (chip_info.features & CHIP_FEATURE_BLE) ? "BLE" : "",
           (chip_info.features & CHIP_FEATURE_IEEE802154) ? ", 802.15.4 (Zigbee/Thread)" : "");

    unsigned major_rev = chip_info.revision / 100;
    unsigned minor_rev = chip_info.revision % 100;
    printf("silicon revision v%d.%d, ", major_rev, minor_rev);
    if(esp_flash_get_size(NULL, &flash_size) != ESP_OK) {
        printf("Get flash size failed");
        return;
    }

    printf("%" PRIu32 "MB %s flash\n", flash_size / (uint32_t)(1024 * 1024),
           (chip_info.features & CHIP_FEATURE_EMB_FLASH) ? "embedded" : "external");

    printf("Minimum free heap size: %" PRIu32 " bytes\n", esp_get_minimum_free_heap_size());
}

static inline void set_servo_pwm(uint8_t channel, int16_t angle)
{
    ESP_LOGI(TAG_PWM, "set %d angle: %d", channel, angle);
    uint32_t pwm = RA_SERVO_PWM_RANGE * (uint32_t)angle / RA_SERVO_ANGLE_RANGE + RA_SERVO_PWM_MIN;
    pca9685_set_channel_pwm(channel, (uint16_t) pwm);
}

static inline void move_servo(uint32_t index, int16_t offset)
{
    servo_t *s = &servos[index];
    s->target_angle = s->target_angle + offset;
    if (s->target_angle < s->min_angle) {
        s->target_angle = s->min_angle;
    }
    if (s->target_angle > s->max_angle) {
        s->target_angle = s->max_angle;
    }
    set_servo_pwm(index, s->target_angle);
}

static void init_servos()
{
    // 旋转底座舵机A:
    servos[RA_SERVO_A].initial_angle = servos[RA_SERVO_A].target_angle = 90;
    servos[RA_SERVO_A].min_angle = 20;
    servos[RA_SERVO_A].max_angle = 160;
    // B轴舵机B:
    servos[RA_SERVO_B].initial_angle = servos[RA_SERVO_B].target_angle = 90;
    servos[RA_SERVO_B].min_angle = 70;
    servos[RA_SERVO_B].max_angle = 110;
    // CD连杆舵机C:
    servos[RA_SERVO_C].initial_angle = servos[RA_SERVO_C].target_angle = 90;
    servos[RA_SERVO_C].min_angle = 45;
    servos[RA_SERVO_C].max_angle = 135;
    // 夹爪轴舵机D:
    servos[RA_SERVO_D].initial_angle = servos[RA_SERVO_D].target_angle = 90;
    servos[RA_SERVO_D].min_angle = 70;
    servos[RA_SERVO_D].max_angle = 110;
    // 读取实际安装角度并调整:
    // TODO:
    // 重置所有舵机:
    for (uint32_t i=0; i<4; i++) {
        set_servo_pwm(i, servos[i].target_angle);
    }
}

// 摇杆输入的x,y范围是:左=0 ~ 中=0x8000 ~ 右=0xffff
// 将其转换为偏移量 左=-8 ~ 中=0 ~ 右=8
static inline int16_t get_offset(uint16_t v) {
    if (v <= 0x7000) {
        // 返回 -8 ~ -1:
        int16_t offset = (int16_t)((0x8000 - v) >> 12);
        return -offset;
    } else if (v >= 0x8fff) {
        // 返回 1 ~ 8:
        return (int16_t)((v - 0x7fff) >> 12);
    }
    return 0;
}

void control_task(void *pvParameters)
{
    // 从队列取出手柄信号并控制舵机:
    ctrl_input_data_t input;
    for (;;) {
        if (pdTRUE == xQueueReceive(ctrl_input_queue, &input, 0)) {
            ESP_LOGI("Queue", "Receive input: %d", input.buttons);
            // 判断左右移动:
            int16_t left = get_offset(input.left_stick_x);
            if (left != 0) {
                move_servo(RA_SERVO_A, left);
            }
            // 判断前后移动:
            int16_t forward = get_offset(input.left_stick_y);
            if (forward != 0) {
                move_servo(RA_SERVO_B, -forward);
            }
            // 判断上下移动:
            int16_t up = get_offset(input.right_stick_y);
            if (up != 0) {
                move_servo(RA_SERVO_C, -up);
            }
            // L1合上夹爪，R1松开夹爪:
            if ((input.buttons & XBOX_BUTTON_L1) == XBOX_BUTTON_L1) {
                move_servo(RA_SERVO_D, -5);
            } else if ((input.buttons & XBOX_BUTTON_R1) == XBOX_BUTTON_R1) {
                move_servo(RA_SERVO_D, 5);
            }
            // 同时按下VIEW和MENU则保存当前位置:
            if ((input.ex_buttons & (XBOX_EX_BUTTON_VIEW | XBOX_EX_BUTTON_MENU)) == (XBOX_EX_BUTTON_VIEW | XBOX_EX_BUTTON_MENU)) {
                ESP_LOGI(TAG_HID, "save current position as initial.");
            }
        }
        // 每读取一次输入后，等待100ms，即每秒仅允许10次输入
        vTaskDelay(100 / portTICK_PERIOD_MS);
    }
}

void app_main(void)
{
    ESP_LOGI(TAG_HID, "starting robotic arm...");
    init_chip();
    vTaskDelay(2000 / portTICK_PERIOD_MS);
    memset(&ctrl_input_data, 0, sizeof(ctrl_input_data_t));
    ctrl_input_queue = xQueueCreate(1, sizeof(ctrl_input_data_t));

    init_i2c_master();
    pca9685_set_adress(RA_I2C_ADDRESS);
    pca9685_reset();
    pca9685_set_freq(RA_PWM_FREQ);
    ESP_LOGI(TAG_PWM, "pca9685 init ok.");
    init_servos();

    char bda_str[18] = {0};
    esp_err_t ret;
#if HID_HOST_MODE == HIDH_IDLE_MODE
    ESP_LOGE(TAG_HID, "Please turn on BT HID host or BLE!");
    return;
#endif
    ret = nvs_flash_init();
    if (ret == ESP_ERR_NVS_NO_FREE_PAGES || ret == ESP_ERR_NVS_NEW_VERSION_FOUND) {
        ESP_ERROR_CHECK(nvs_flash_erase());
        ret = nvs_flash_init();
    }
    ESP_ERROR_CHECK( ret );
    ESP_LOGI(TAG_HID, "setting hid gap, mode:%d", HID_HOST_MODE);
    ESP_ERROR_CHECK( esp_hid_gap_init(HID_HOST_MODE) );
#if CONFIG_BT_BLE_ENABLED
    ESP_ERROR_CHECK( esp_ble_gattc_register_callback(esp_hidh_gattc_event_handler) );
#endif /* CONFIG_BT_BLE_ENABLED */
    esp_hidh_config_t config = {
        .callback = hidh_callback,
        .event_stack_size = 4096,
        .callback_arg = NULL,
    };
    ESP_ERROR_CHECK( esp_hidh_init(&config) );

    ESP_LOGI(TAG_HID, "Own address:[%s]", bda2str((uint8_t *)esp_bt_dev_get_address(), bda_str, sizeof(bda_str)));
#if CONFIG_BT_NIMBLE_ENABLED
    /* XXX Need to have template for store */
    ble_store_config_init();

    ble_hs_cfg.store_status_cb = ble_store_util_status_rr;
	/* Starting nimble task after gatts is initialized*/
    ret = esp_nimble_enable(ble_hid_host_task);
    if (ret) {
        ESP_LOGE(TAG_HID, "esp_nimble_enable failed: %d", ret);
    }
#endif
    xTaskCreate(&hid_scan_task, "hid_scan_task", 6 * 1024, NULL, 2, NULL);
    xTaskCreate(&control_task, "control_task", 4 * 1024, NULL, 2, NULL);
}

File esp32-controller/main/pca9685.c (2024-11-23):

/***************************************************
  Copied and modified from: https://github.com/brainelectronics/esp32-pca9685/blob/master/components/pca9685/pca9685.c

  This is a library for the PCA9685 LED PWM Driver

  This chip is connected via I2C, 2 pins are required to interface. The PWM frequency is set for all pins, the PWM for each individually. The set PWM is active as long as the chip is powered.

  Written by Jonas Scharpf <jonas@brainelectronics.de>
  BSD license, all text above must be included in any redistribution
 ****************************************************/

#include "pca9685.h"
#include <freertos/FreeRTOS.h>
#include <driver/i2c.h>
#include <string.h>
#include <stdio.h>
#include <stdlib.h>
#include <stdint.h>
#include <math.h>
#include "esp_err.h"
#include <errno.h>
#include "esp_log.h"
#include "esp_system.h"

// Register addresses from data sheet
#define PCA9685_MODE1_REG               (uint8_t)0x00
#define PCA9685_MODE2_REG               (uint8_t)0x01
#define PCA9685_SUBADR1_REG             (uint8_t)0x02
#define PCA9685_SUBADR2_REG             (uint8_t)0x03
#define PCA9685_SUBADR3_REG             (uint8_t)0x04
#define PCA9685_ALLCALL_REG             (uint8_t)0x05
#define PCA9685_LED0_REG                (uint8_t)0x06          // Start of LEDx regs, 4B per reg, 2B on phase, 2B off phase, little-endian
#define PCA9685_PRESCALE_REG            (uint8_t)0xFE
#define PCA9685_ALLLED_REG              (uint8_t)0xFA

// Mode1 register values
#define PCA9685_MODE1_RESTART           (uint8_t)0x80
#define PCA9685_MODE1_EXTCLK            (uint8_t)0x40
#define PCA9685_MODE1_AUTOINC           (uint8_t)0x20
#define PCA9685_MODE1_SLEEP             (uint8_t)0x10
#define PCA9685_MODE1_SUBADR1           (uint8_t)0x08
#define PCA9685_MODE1_SUBADR2           (uint8_t)0x04
#define PCA9685_MODE1_SUBADR3           (uint8_t)0x02
#define PCA9685_MODE1_ALLCALL           (uint8_t)0x01

// Mode2 register values
#define PCA9685_MODE2_OUTDRV_TPOLE      (uint8_t)0x04
#define PCA9685_MODE2_INVRT             (uint8_t)0x10
#define PCA9685_MODE2_OUTNE_TPHIGH      (uint8_t)0x01
#define PCA9685_MODE2_OUTNE_HIGHZ       (uint8_t)0x02
#define PCA9685_MODE2_OCH_ONACK         (uint8_t)0x08

#define PCA9685_SW_RESET                (uint8_t)0x06          // Sent to address 0x00 to reset all devices on Wire line
#define PCA9685_PWM_FULL                (uint16_t)0x1000    // Special value for full on/full off LEDx modes
#define PCA9685_PWM_MASK                (uint16_t)0x0FFF    // Mask for 12-bit/4096 possible phase positions

#define PCA9685_CHANNEL_COUNT           (uint8_t)16

#define ACK_CHECK_EN    0x1     /*!< I2C master will check ack from slave */
#define ACK_CHECK_DIS   0x0     /*!< I2C master will not check ack from slave */
#define ACK_VAL         0x0     /*!< I2C ack value */
#define NACK_VAL        0x1     /*!< I2C nack value */

#define LED0_ON_L       0x6     /*!< LED0 output and brightness control byte 0 */
#define LED0_ON_H       0x7     /*!< LED0 output and brightness control byte 1 */
#define LED0_OFF_L      0x8     /*!< LED0 output and brightness control byte 2 */
#define LED0_OFF_H      0x9     /*!< LED0 output and brightness control byte 3 */

#define ALLLED_ON_L     0xFA    /*!< load all the LEDn_ON registers, byte 0 (turn 0-7 channels on) */
#define ALLLED_ON_H     0xFB    /*!< load all the LEDn_ON registers, byte 1 (turn 8-15 channels on) */
#define ALLLED_OFF_L    0xFC    /*!< load all the LEDn_OFF registers, byte 0 (turn 0-7 channels off) */
#define ALLLED_OFF_H    0xFD    /*!< load all the LEDn_OFF registers, byte 1 (turn 8-15 channels off) */
#define CLOCK_FREQ      25000000  /*!< 25MHz default osc clock */

static const char *TAG = "PCA9685";

// default address is 0x40:
static uint8_t PCA9685_ADDR = 0x40;

/**
 * Set the adress of PCA9685.
 */
void pca9685_set_adress(uint8_t addr)
{
    PCA9685_ADDR = addr;
    ESP_LOGI(TAG, "init: address = 0x%x.", PCA9685_ADDR);
}

/**
 * Write two 16 bit values to the same register.
 */
esp_err_t generic_write_i2c_register_two_words(uint8_t regaddr, uint16_t valueOn, uint16_t valueOff)
{
    esp_err_t ret;

    i2c_cmd_handle_t cmd = i2c_cmd_link_create();
    i2c_master_start(cmd);
    i2c_master_write_byte(cmd, (PCA9685_ADDR << 1) | I2C_MASTER_WRITE, ACK_CHECK_EN);
    i2c_master_write_byte(cmd, regaddr, ACK_CHECK_EN);
    i2c_master_write_byte(cmd, valueOn & 0xff, ACK_VAL);
    i2c_master_write_byte(cmd, valueOn >> 8, NACK_VAL);
    i2c_master_write_byte(cmd, valueOff & 0xff, ACK_VAL);
    i2c_master_write_byte(cmd, valueOff >> 8, NACK_VAL);
    i2c_master_stop(cmd);
    ret = i2c_master_cmd_begin(I2C_NUM_0, cmd, 1000 / portTICK_PERIOD_MS);
    i2c_cmd_link_delete(cmd);

    return ret;
}

/**
 * Write a 16 bit value to a register.
 */
esp_err_t generic_write_i2c_register_word(uint8_t regaddr, uint16_t value)
{
    esp_err_t ret;

    i2c_cmd_handle_t cmd = i2c_cmd_link_create();
    i2c_master_start(cmd);
    i2c_master_write_byte(cmd, (PCA9685_ADDR << 1) | I2C_MASTER_WRITE, ACK_CHECK_EN);
    i2c_master_write_byte(cmd, regaddr, ACK_CHECK_EN);
    i2c_master_write_byte(cmd, value & 0xff, ACK_VAL);
    i2c_master_write_byte(cmd, value >> 8, NACK_VAL);
    i2c_master_stop(cmd);
    ret = i2c_master_cmd_begin(I2C_NUM_0, cmd, 1000 / portTICK_PERIOD_MS);
    i2c_cmd_link_delete(cmd);

    return ret;
}

/**
 * Write a 8 bit value to a register.
 */
esp_err_t generic_write_i2c_register(uint8_t regaddr, uint8_t value)
{
    esp_err_t ret;

    i2c_cmd_handle_t cmd = i2c_cmd_link_create();
    i2c_master_start(cmd);
    i2c_master_write_byte(cmd, (PCA9685_ADDR << 1) | I2C_MASTER_WRITE, ACK_CHECK_EN);
    i2c_master_write_byte(cmd, regaddr, ACK_CHECK_EN);
    i2c_master_write_byte(cmd, value, NACK_VAL);
    i2c_master_stop(cmd);
    ret = i2c_master_cmd_begin(I2C_NUM_0, cmd, 1000 / portTICK_PERIOD_MS);
    i2c_cmd_link_delete(cmd);

    return ret;
}

/**
 * Read two 8 bit values from the same register.
 */
esp_err_t generic_read_two_i2c_register(uint8_t regaddr, uint8_t* valueA, uint8_t* valueB)
{
    esp_err_t ret;

    i2c_cmd_handle_t cmd = i2c_cmd_link_create();
    i2c_master_start(cmd);
    i2c_master_write_byte(cmd, (PCA9685_ADDR << 1) | I2C_MASTER_WRITE, ACK_CHECK_EN);
    i2c_master_write_byte(cmd, regaddr, ACK_CHECK_EN);
    i2c_master_stop(cmd);
    ret = i2c_master_cmd_begin(I2C_NUM_0, cmd, 1000 / portTICK_PERIOD_MS);
    i2c_cmd_link_delete(cmd);
    if (ret != ESP_OK) {
        return ret;
    }
    cmd = i2c_cmd_link_create();
    i2c_master_start(cmd);
    i2c_master_write_byte(cmd, PCA9685_ADDR << 1 | I2C_MASTER_READ, ACK_CHECK_EN);
    i2c_master_read_byte(cmd, valueA, ACK_VAL);
    i2c_master_read_byte(cmd, valueB, NACK_VAL);
    i2c_master_stop(cmd);
    ret = i2c_master_cmd_begin(I2C_NUM_0, cmd, 1000 / portTICK_PERIOD_MS);
    i2c_cmd_link_delete(cmd);
    
    return ret;
}
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

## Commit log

2024-11-19 add i2c driver
2024-11-20 add solidworks models
    [BC连杆.SLDPRT, CD连杆.SLDPRT, C轴摇杆.SLDPRT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]
2024-11-23 update model
    [RoboticArm总装配体.SLDASM, 固定底座底部盖板.SLDPRT, 固定底座装配体.SLDASM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]
2024-11-23 add 3d-printable files
    [打印件1.STEP, 打印件2.STEP, 打印件3.STEP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]
2024-11-23 add circuit
2024-11-24 update model.
    [RoboticArm总装配体.SLDASM, 上水平连杆.SLDPRT, 夹爪支架.SLDPRT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]
2024-11-25 fix model
    [BC连杆.SLDPRT, RoboticArm总装配体.SLDASM, 固定底座装配体.SLDASM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]
2024-11-30 add image for esp32-pca9685-servo connection.
2024-12-03 update sw model
    [RoboticArm总装配体.SLDASM]
